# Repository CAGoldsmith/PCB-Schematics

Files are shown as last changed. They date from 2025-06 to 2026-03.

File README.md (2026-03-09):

# Drosophibot II PCBs
Power and signal PCBs for the biomimetic fruit fly robot Drosophibot II. More information about Drosophibot II can be found in [Goldsmith et al. 2024](https://iopscience.iop.org/article/10.1088/1748-3190/ad80ec) and [Goldsmith 2025](https://researchrepository.wvu.edu/etd/12842/). CAD files for the robot can be found in the [`Drosophibot-II-CAD`](https://github.com/CAGoldsmith/Drosophibot-II-CAD) repository.

This repository contains:
- ZIP files of the Gerber and drill files necessary to manufacture each board
- PDFs with renders and schematics of the boards
- A `.f3z` file of each board containing the design files from Fusion

## Board functions
### 18 Position OpenCM MUX
An 18 position demultiplexer (routing 18 signals into 6 analog ports) for the Robotis OpenCM9.04 microcontroller. Designed to sit on top of the microcontroller as a shield.

### 36 Position OpenCM MUX
A 36 position demultiplexer (routing 36 signals into 6 analog ports, one for each robot leg) for the Robotis OpenCM9.04 microcontroller. Designed to sit on top of the microcontroller as a shield. Additionally includes multiplexing of the board's I2C ports to route the signal to each leg.

### Six Strain Amplifier
Board intended to amplify and route six analog strain signals, as well as digitally calibrate the rest level of each signal. It contains a Wheatstone bridge circuit for each signal with a digital-potentiometer (digipot) included for bridge balancing via I2C connection from the robot's microcontroller. Each strain signal is then routed into an instrumentation amplifier for amplification before being output. Analog switches are used to multiplex the I2C signal to one half of the board at a time (necessitated by the limited possible unique digipot IDs).  

### Drosophibot Power Board
Board to supply power from the offboard power supply and route the Serial control signal from the robot's computer to all of the robot's actuators. Includes power indicator LEDs as well as removable shunts to easily add/remove power to each leg.

## Editing in Autodesk Fusion 360
Download the relevant board's `.f3z` file and open it in Fusion to import the design files. 

## Manufacturing
Download the "<board name>_CamFiles" zip file for the desired board in the board's "CAMOutputs" folder. For example, for the 36 Position OpenCM MUX, the required file would be "36PosMUX_CamFiles.zip." All boards were designed with professional PCB manufacturing in mind, so the Design Rules may need to be changed in Autodesk for places with less capability (e.g., campus makerspaces).

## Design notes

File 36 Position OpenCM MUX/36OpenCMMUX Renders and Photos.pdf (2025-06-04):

B)

A)

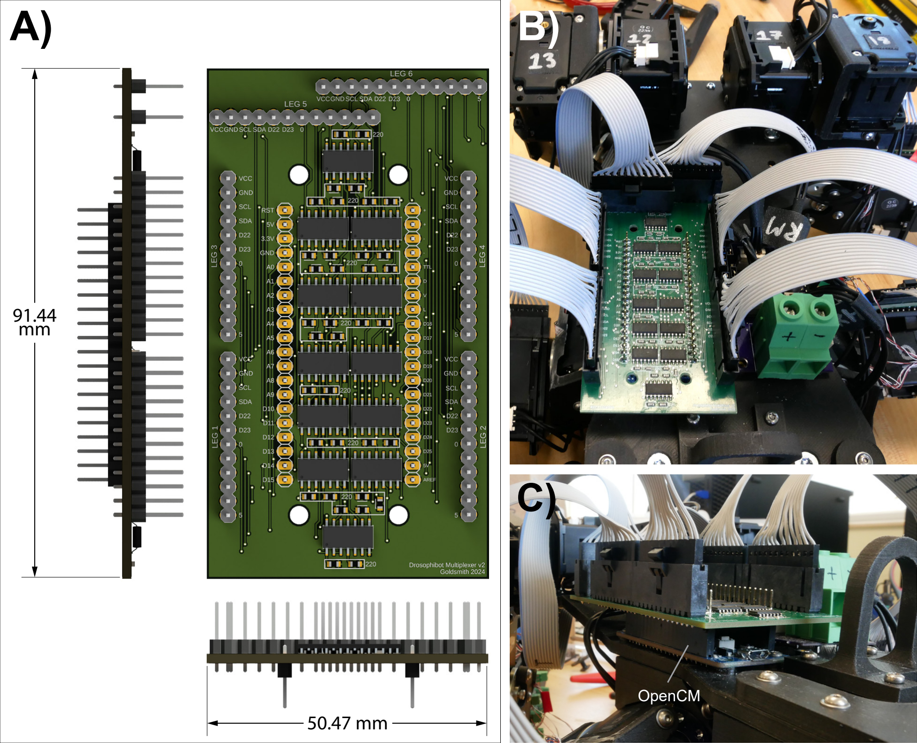
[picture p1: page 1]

Image of how deMUX slots onto OpenCM

50.47 mm

91.44
mm

C)

OpenCM

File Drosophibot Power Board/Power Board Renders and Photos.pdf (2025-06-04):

B)

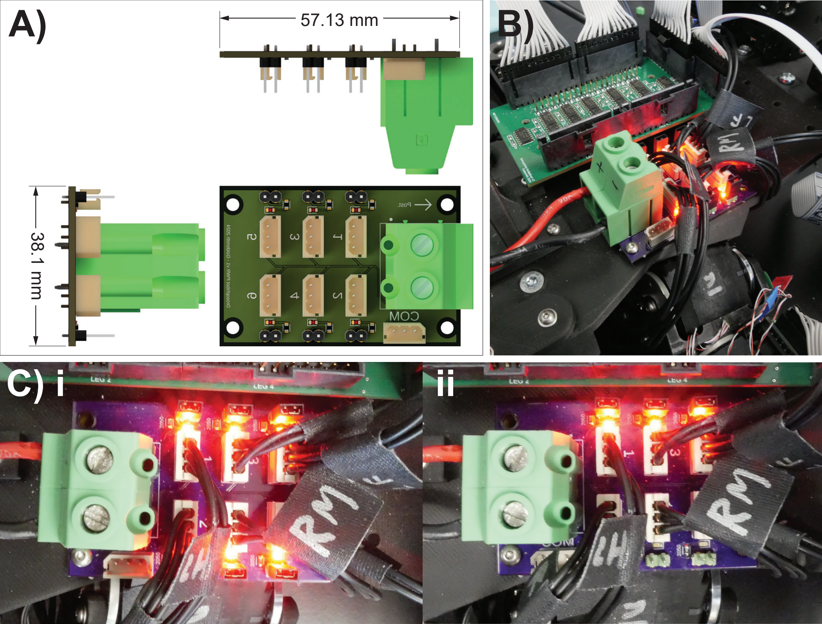
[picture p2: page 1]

38.1 mm

A) 57.13 mm
C) i | ii

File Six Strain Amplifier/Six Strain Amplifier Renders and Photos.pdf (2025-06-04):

A) B)

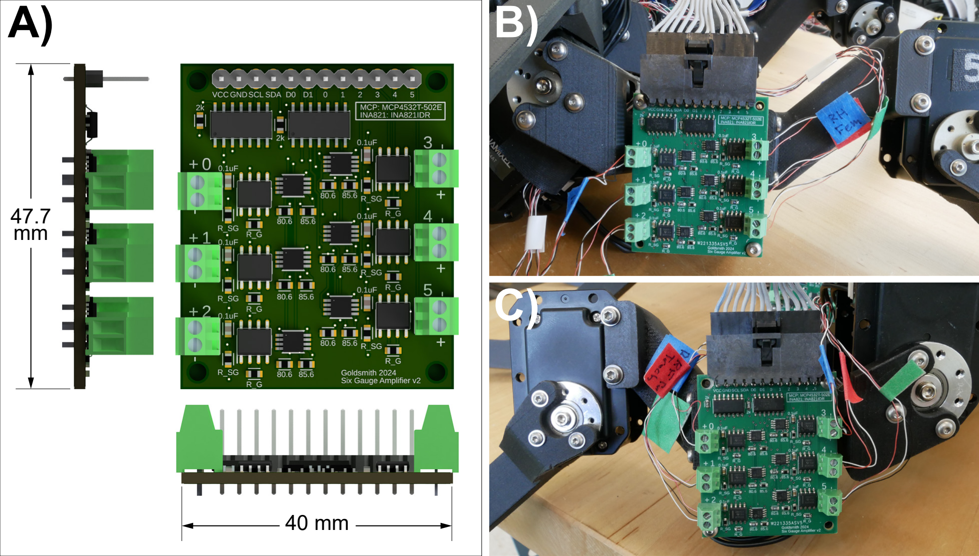
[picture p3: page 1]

47.7
mm

40 mm

C)

Image of circuit board on
multiple legs

C)

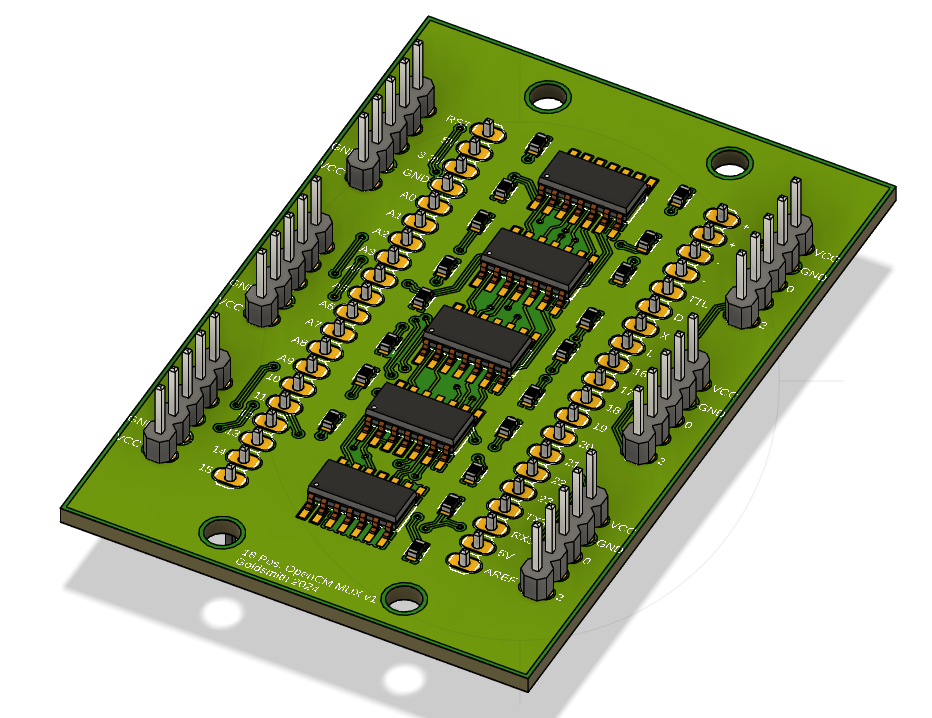
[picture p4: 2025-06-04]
18 Position OpenCM MUX/18 Pos OpenCM MUX Top Render.png

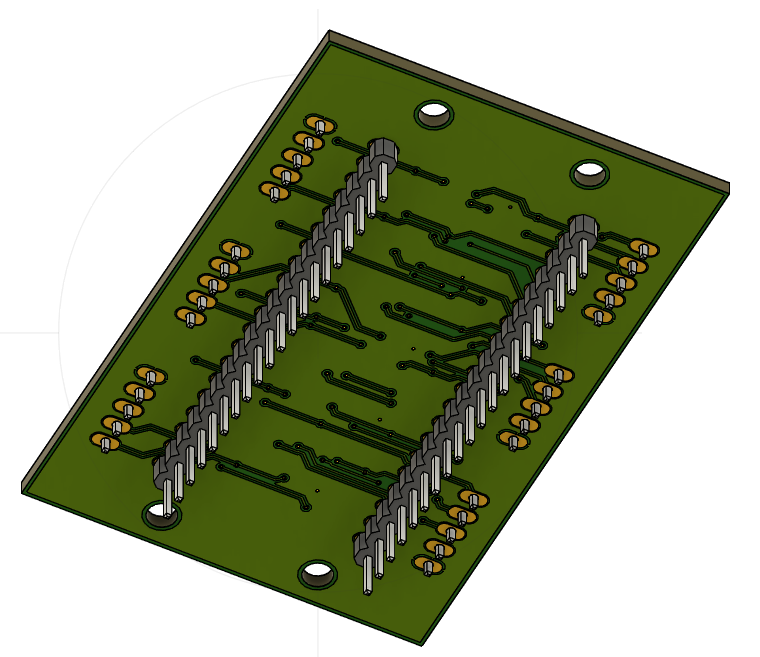
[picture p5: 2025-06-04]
18 Position OpenCM MUX/18 Pos OpenCM MUX Bottom Render.png

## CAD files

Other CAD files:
Drosophibot Power Board/Drosophibot Power Board v44.f3z

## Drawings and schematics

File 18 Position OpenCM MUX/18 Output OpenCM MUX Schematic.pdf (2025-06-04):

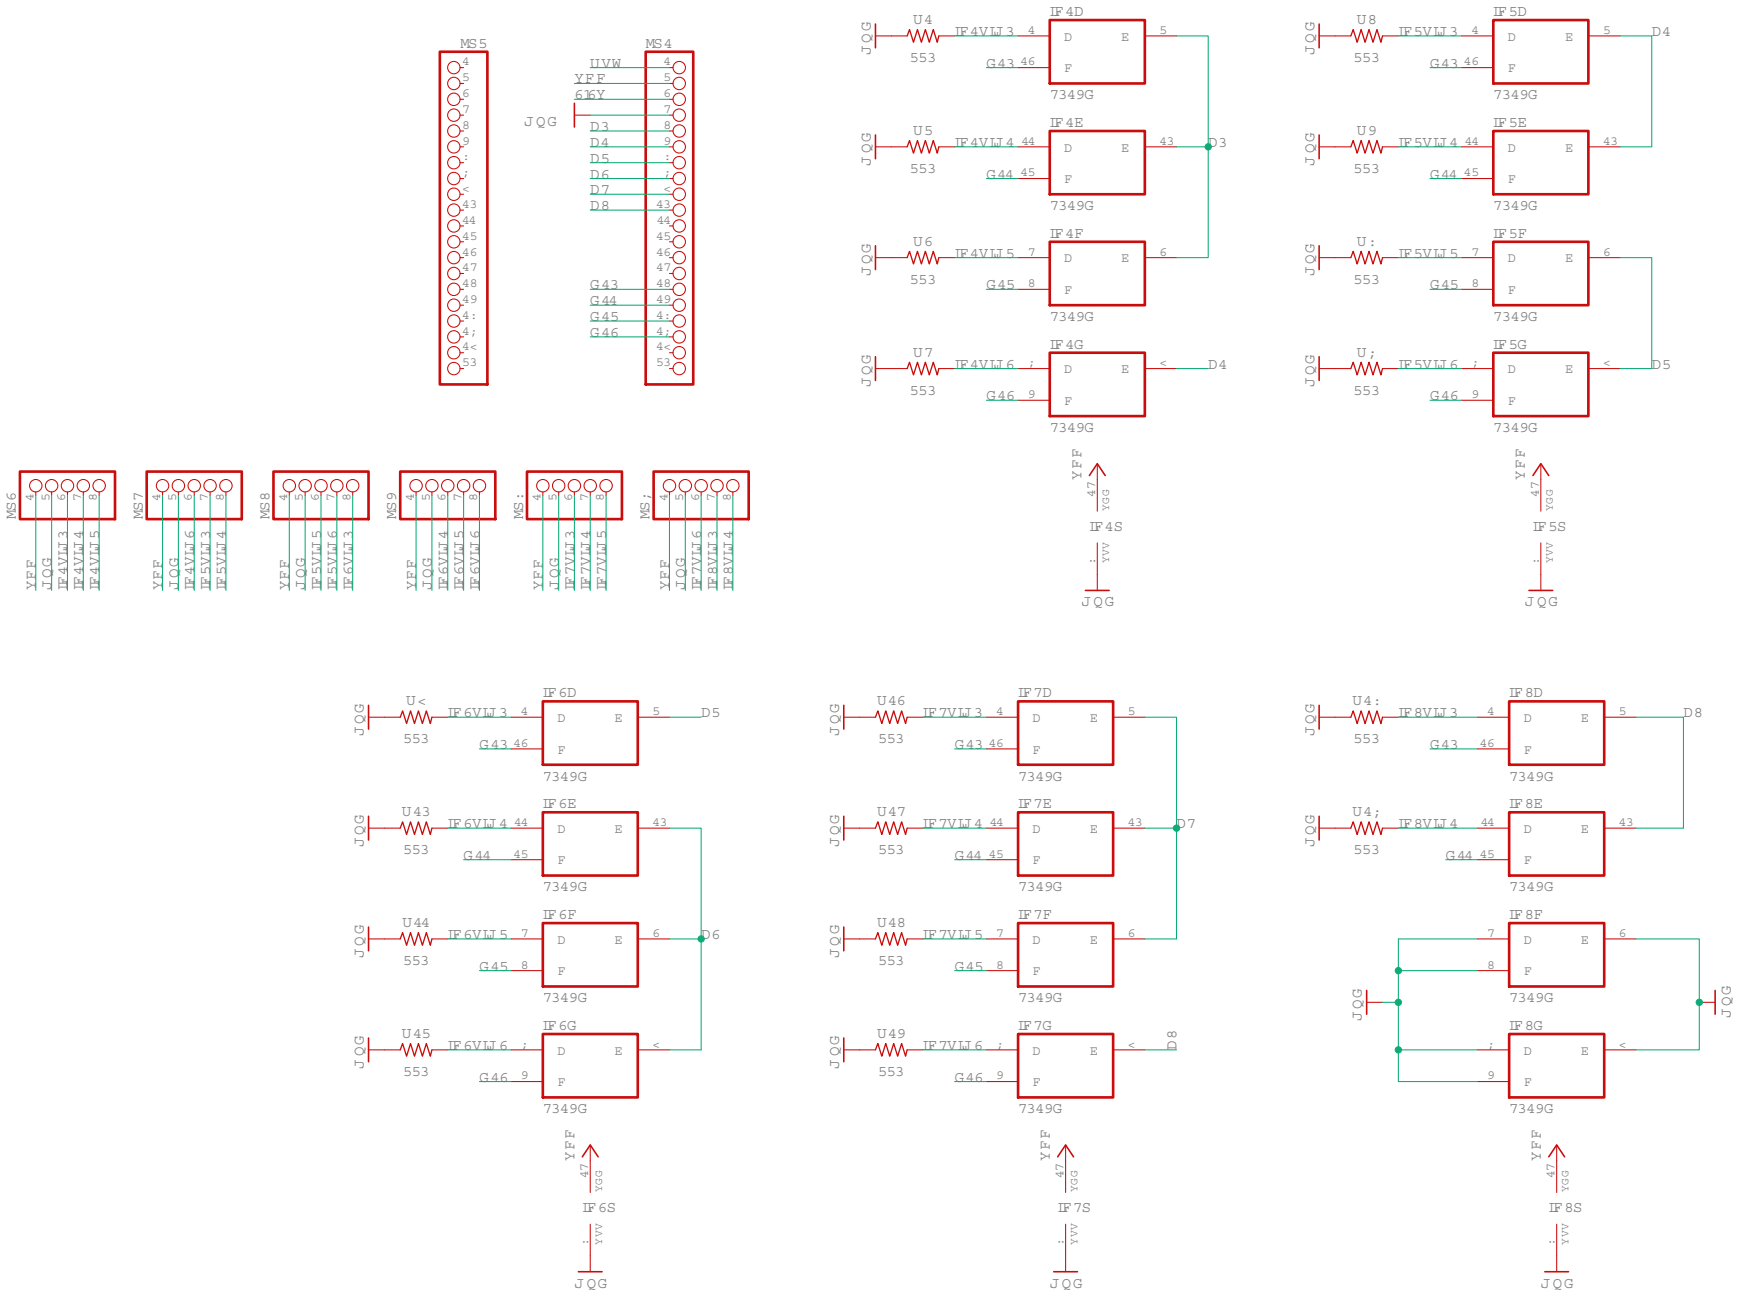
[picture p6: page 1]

GND GND

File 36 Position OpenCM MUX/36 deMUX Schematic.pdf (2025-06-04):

## 36 INPUT DEMUX CIRCUIT

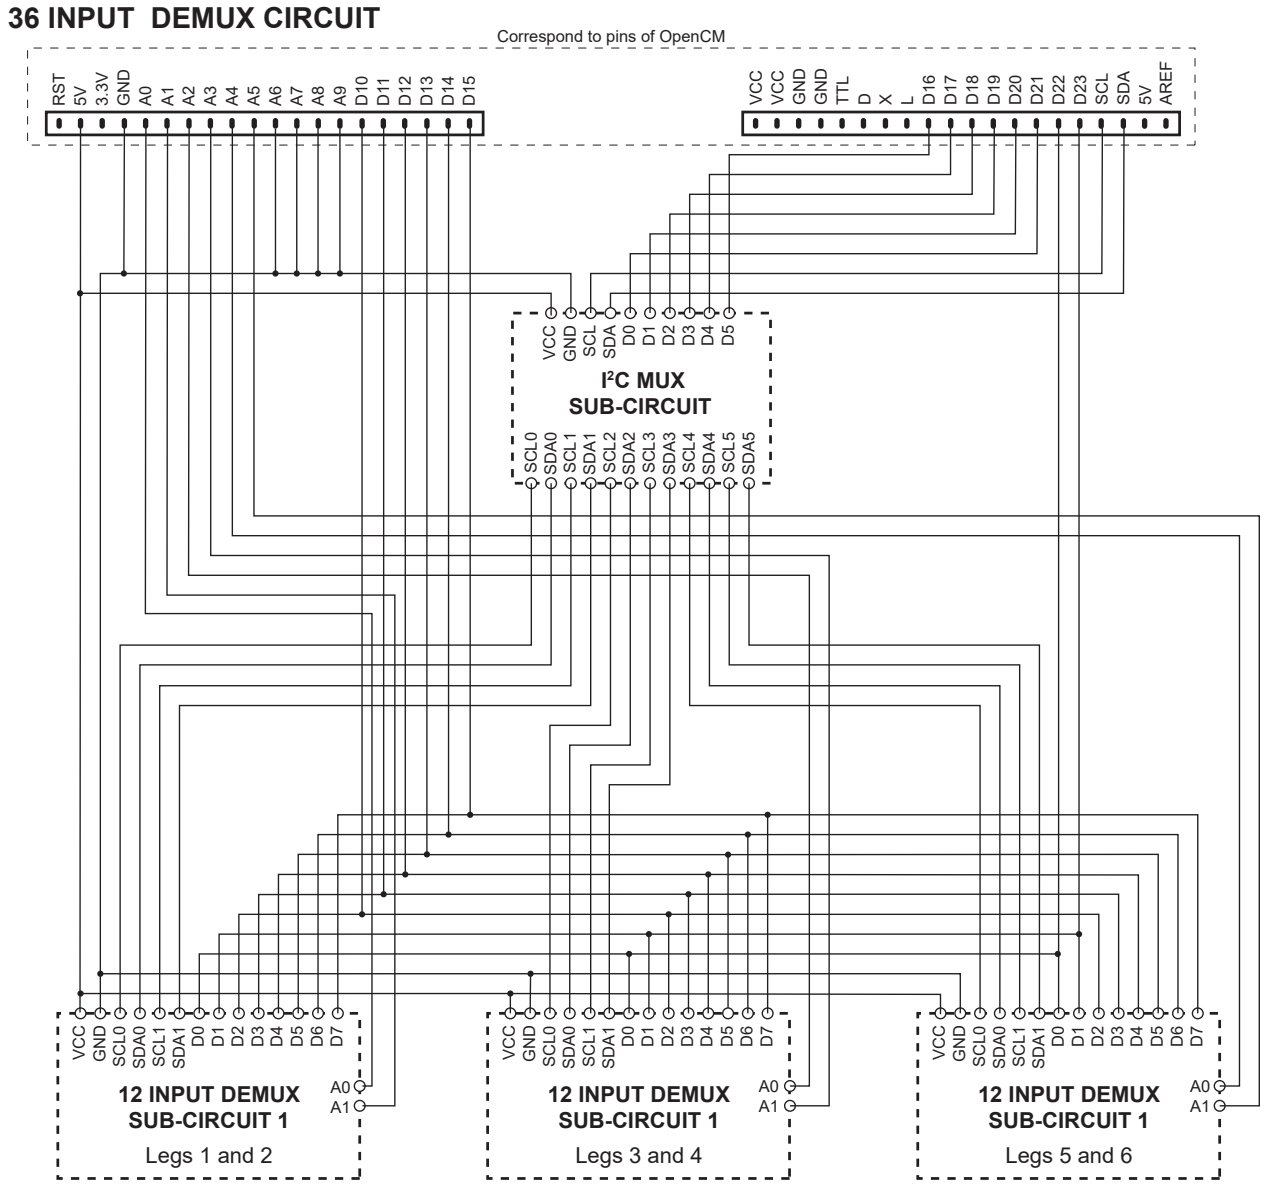
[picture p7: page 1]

Correspond to pins of OpenCM

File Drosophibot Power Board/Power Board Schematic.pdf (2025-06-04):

# DROSOPHIBOT II POWER SUPPLY BOARD

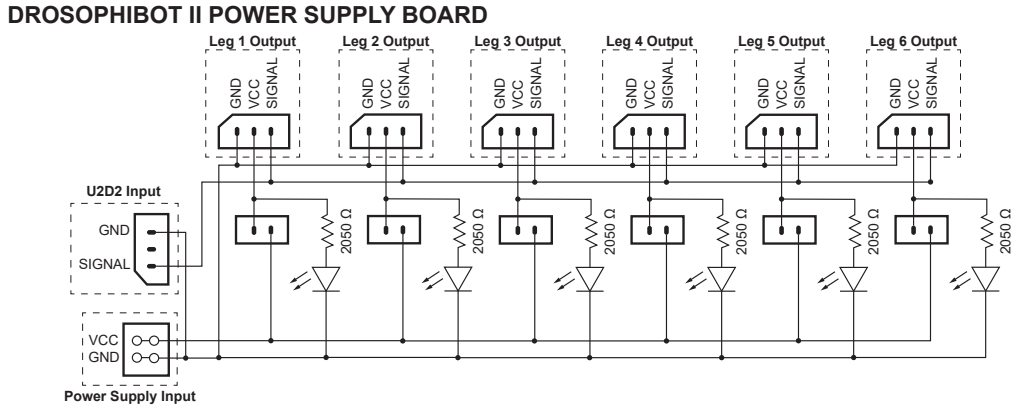
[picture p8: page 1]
GND; SIGNAL; GND VCC; VCC GND; U2D2 Input; Leg 1 Output; Leg 2 Output; Leg 3 Output; Leg 4 Output; Leg 5 Output; Leg 6 Output

Power Supply Input

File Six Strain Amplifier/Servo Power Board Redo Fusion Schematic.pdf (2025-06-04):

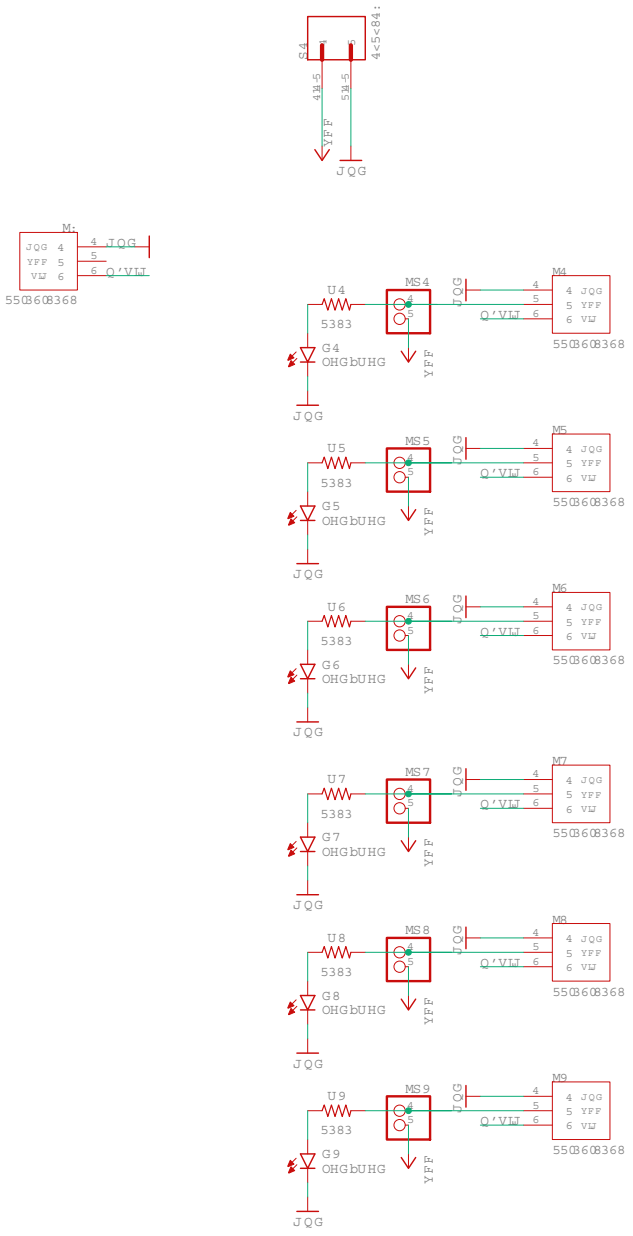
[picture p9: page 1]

GND GND GND

VCC VCC VCC

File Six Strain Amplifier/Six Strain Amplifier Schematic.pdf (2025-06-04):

### SIX STRAIN GAUGE AMPLIFIER

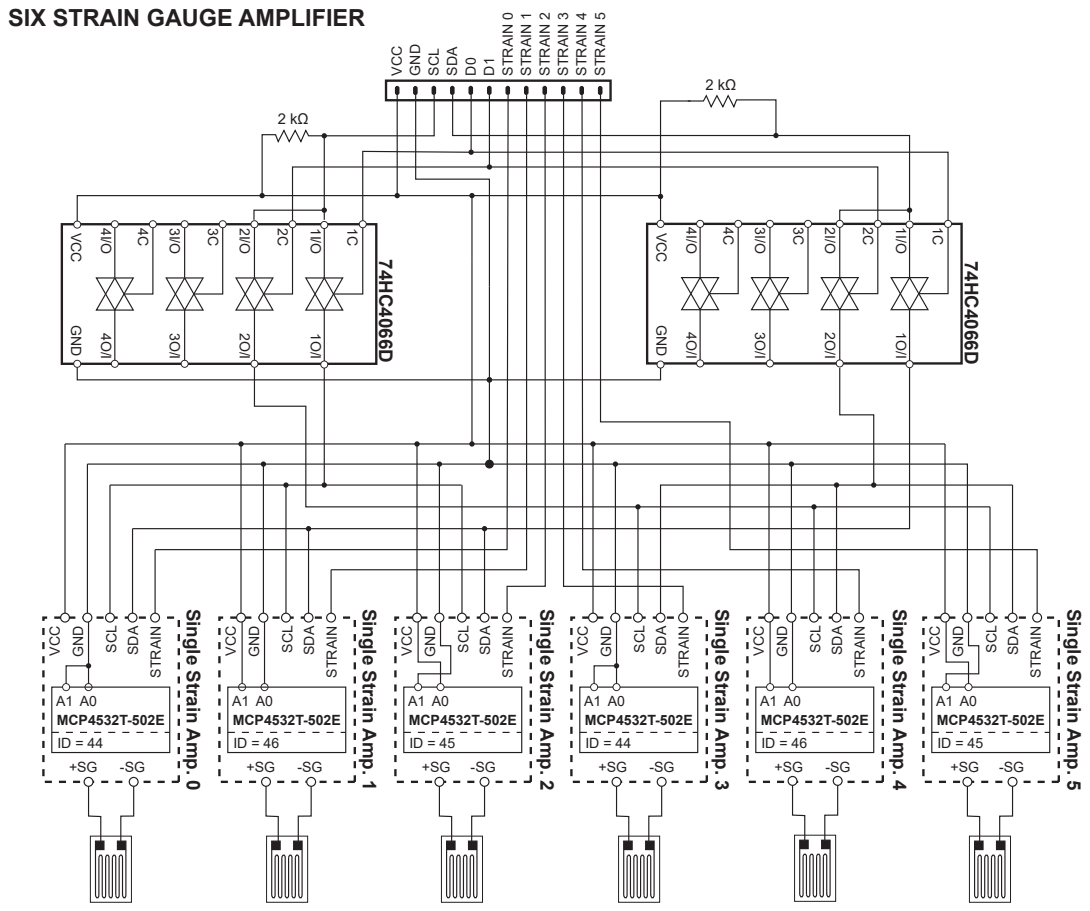
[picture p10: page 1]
VCC; GND; SCL; SDA; STRAIN; MCP4532T-502E; GND SCL; SDA D0; STRAIN 0; STRAIN 1; STRAIN 2; STRAIN 3; STRAIN 4; STRAIN 5; VCC GND

Single Strain Amp. 0

Single Strain Amp. 1

Single Strain Amp. 2

Single Strain Amp. 3

Single Strain Amp. 4

Single Strain Amp. 5

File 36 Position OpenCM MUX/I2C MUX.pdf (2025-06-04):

I
2

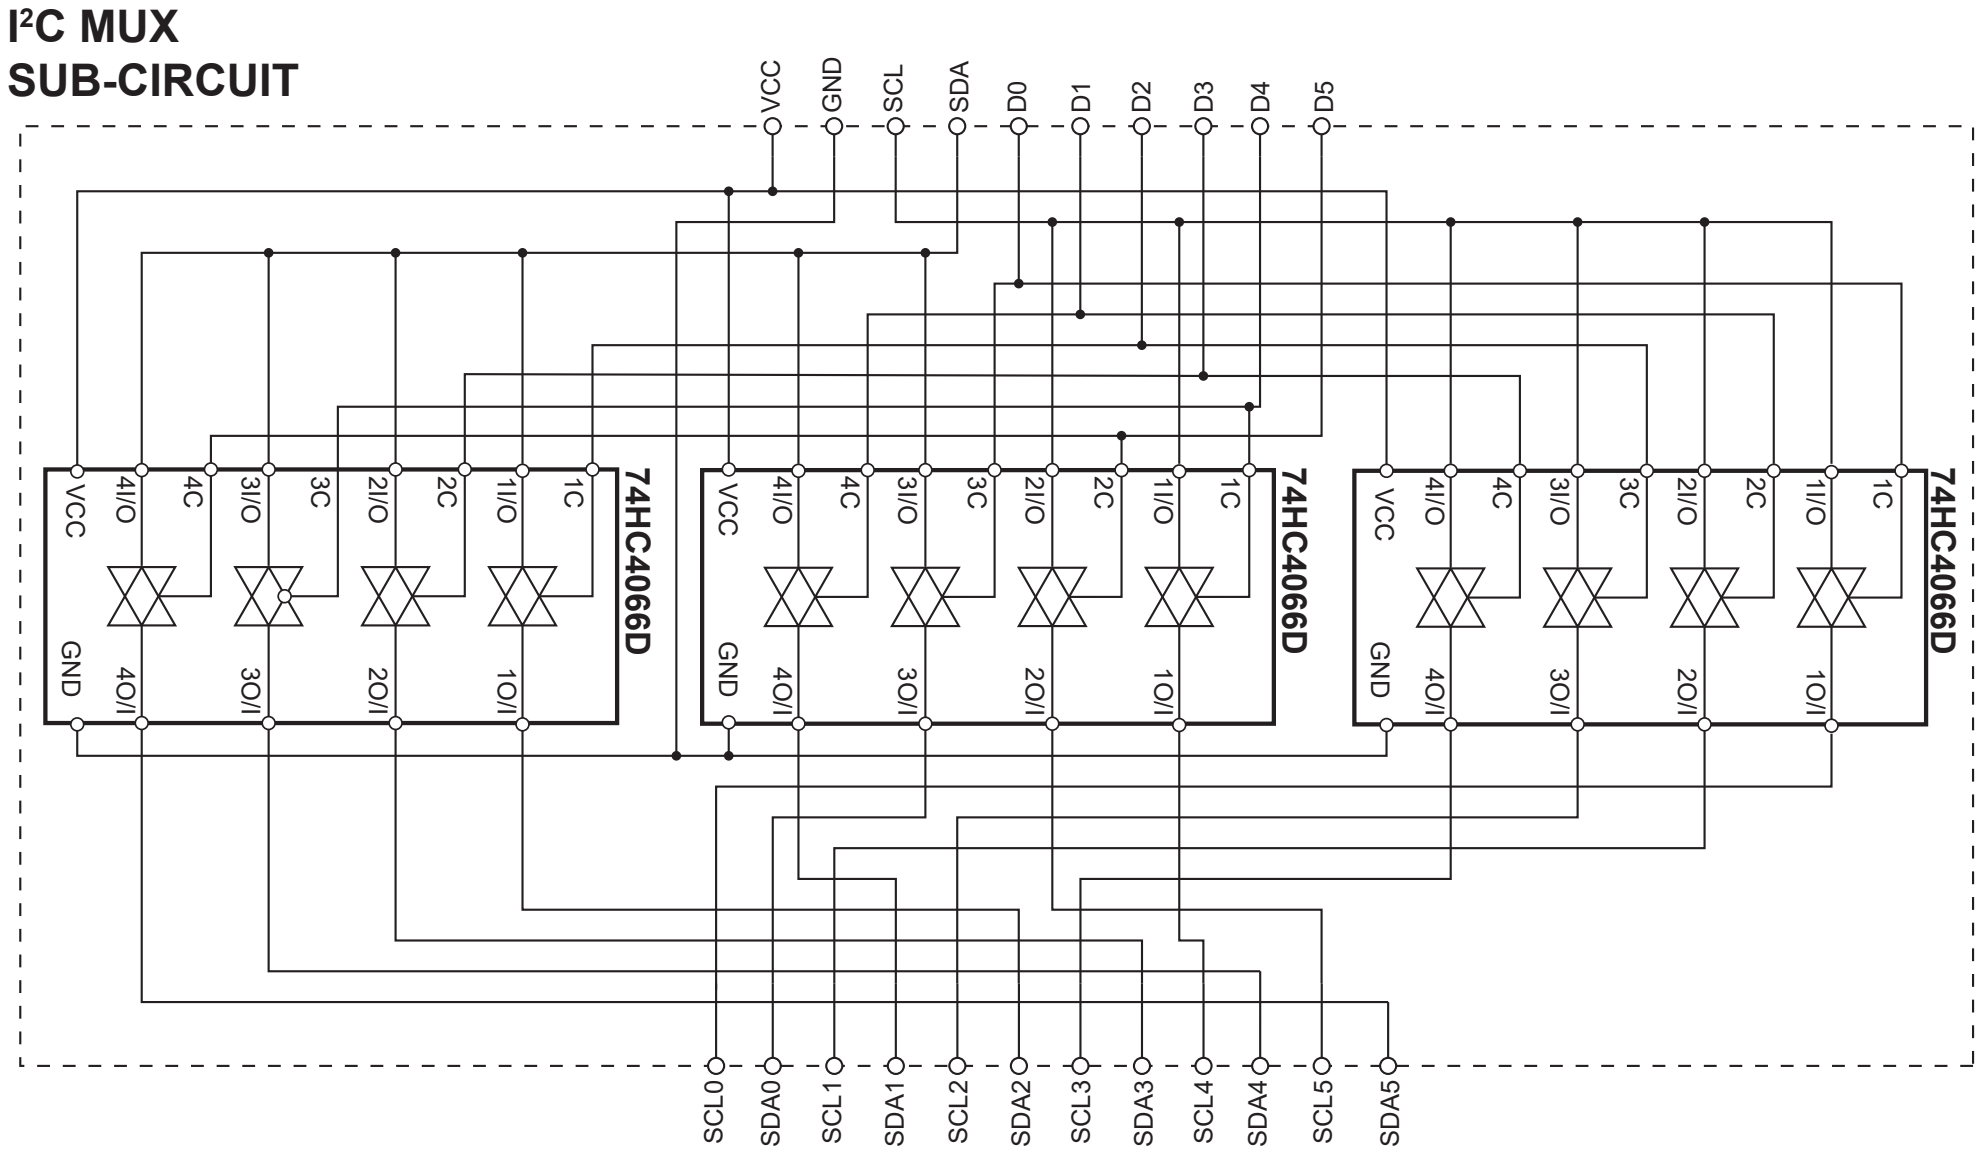
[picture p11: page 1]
C MUX SUB-CIRCUIT; VCC; GND; SCL; SDA; SCL0; SDA0; SCL1; SDA1; SCL2; SDA2; SCL3; SDA3; SCL4; SDA4; SCL5; SDA5; VCC GND

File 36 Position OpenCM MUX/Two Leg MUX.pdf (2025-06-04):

# 12 INPUT DEMUX SUB-CIRCUIT

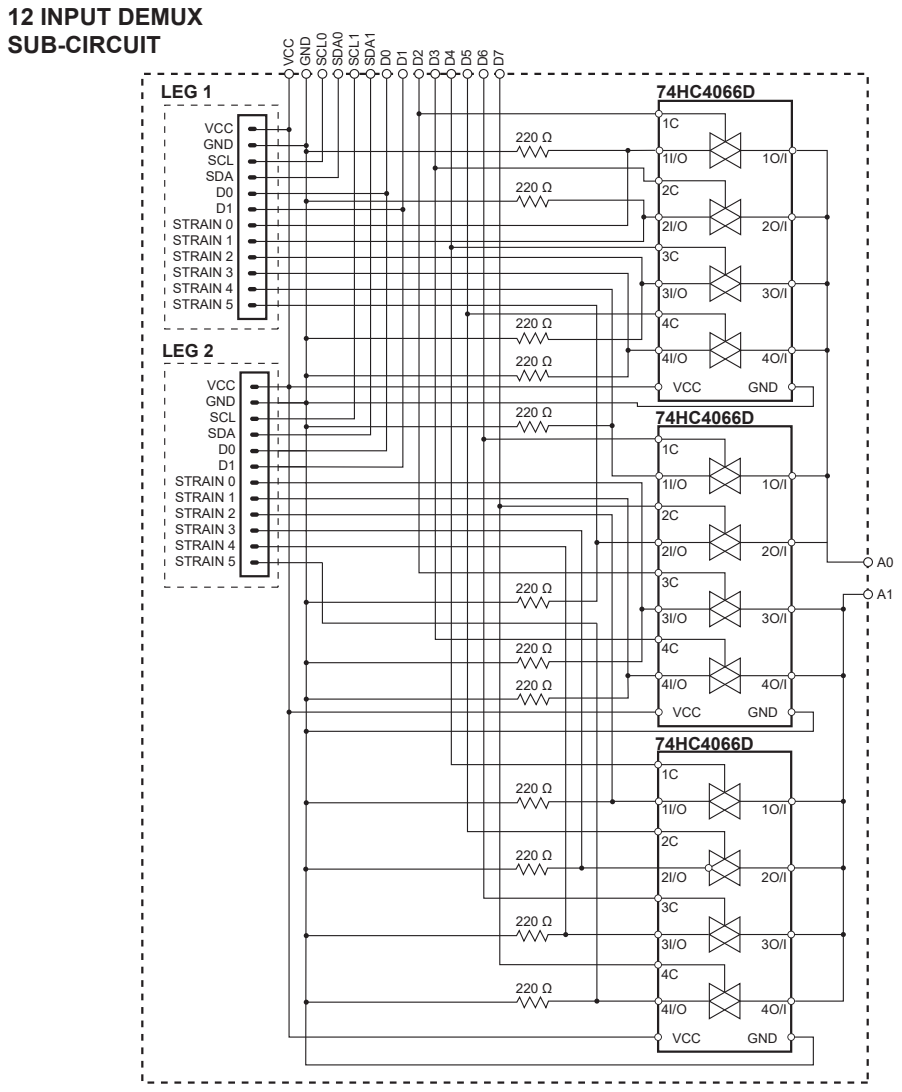
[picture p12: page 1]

LEG 1 | | 74HC4066D

1O/I 2O/I 3O/I 4O/I GND

220 Ω | 4I/O VCC

1O/I
2C

3I/O
4C

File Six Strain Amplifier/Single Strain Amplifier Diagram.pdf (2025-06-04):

# SINGLE STRAIN GAUGE AMPLIFIER SUB-CIRCUIT

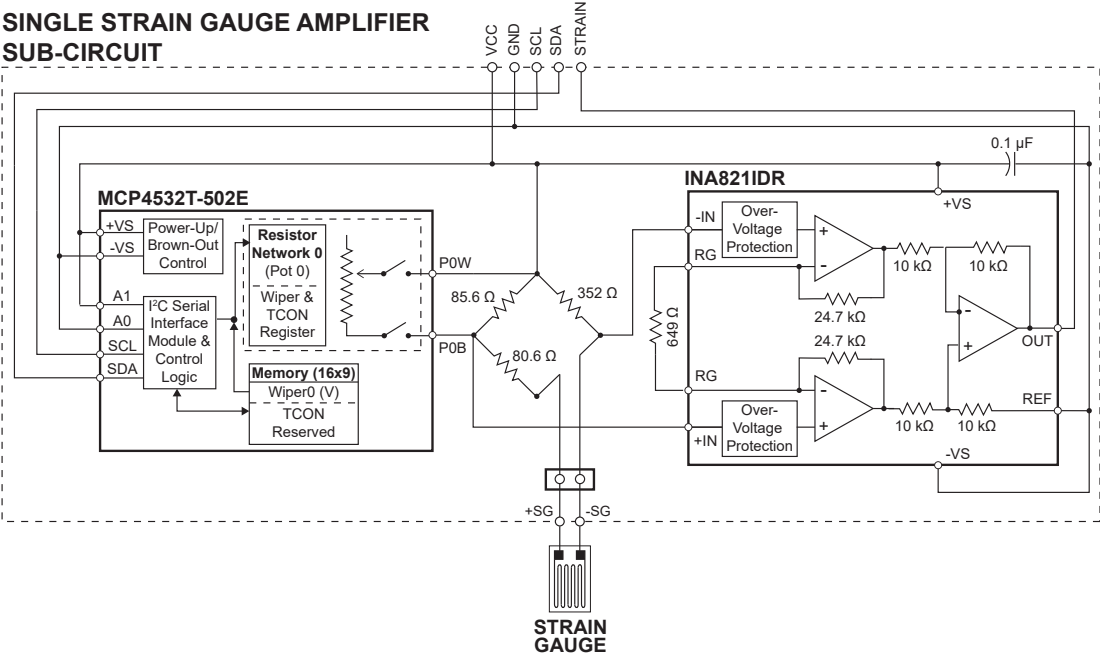
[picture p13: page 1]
Over- Voltage Protection; REF; OUT; INA821IDR; Power-Up/ Brown-Out Control; C Serial Interface Module & Control Logic; A1 A0 SCL; SDA; Memory (16x9); Resistor Network 0 (Pot 0) Wiper & TCON Register; Wiper0 (V) TCON Reserved; MCP4532T-502E; STRAIN GAUGE; VCC; GND; SCL; STRAIN

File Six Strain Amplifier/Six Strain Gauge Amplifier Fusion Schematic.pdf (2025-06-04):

## INA821IDD0008A_L

## M CP4532T-502E/M SM SO P8_M C_M CH-L

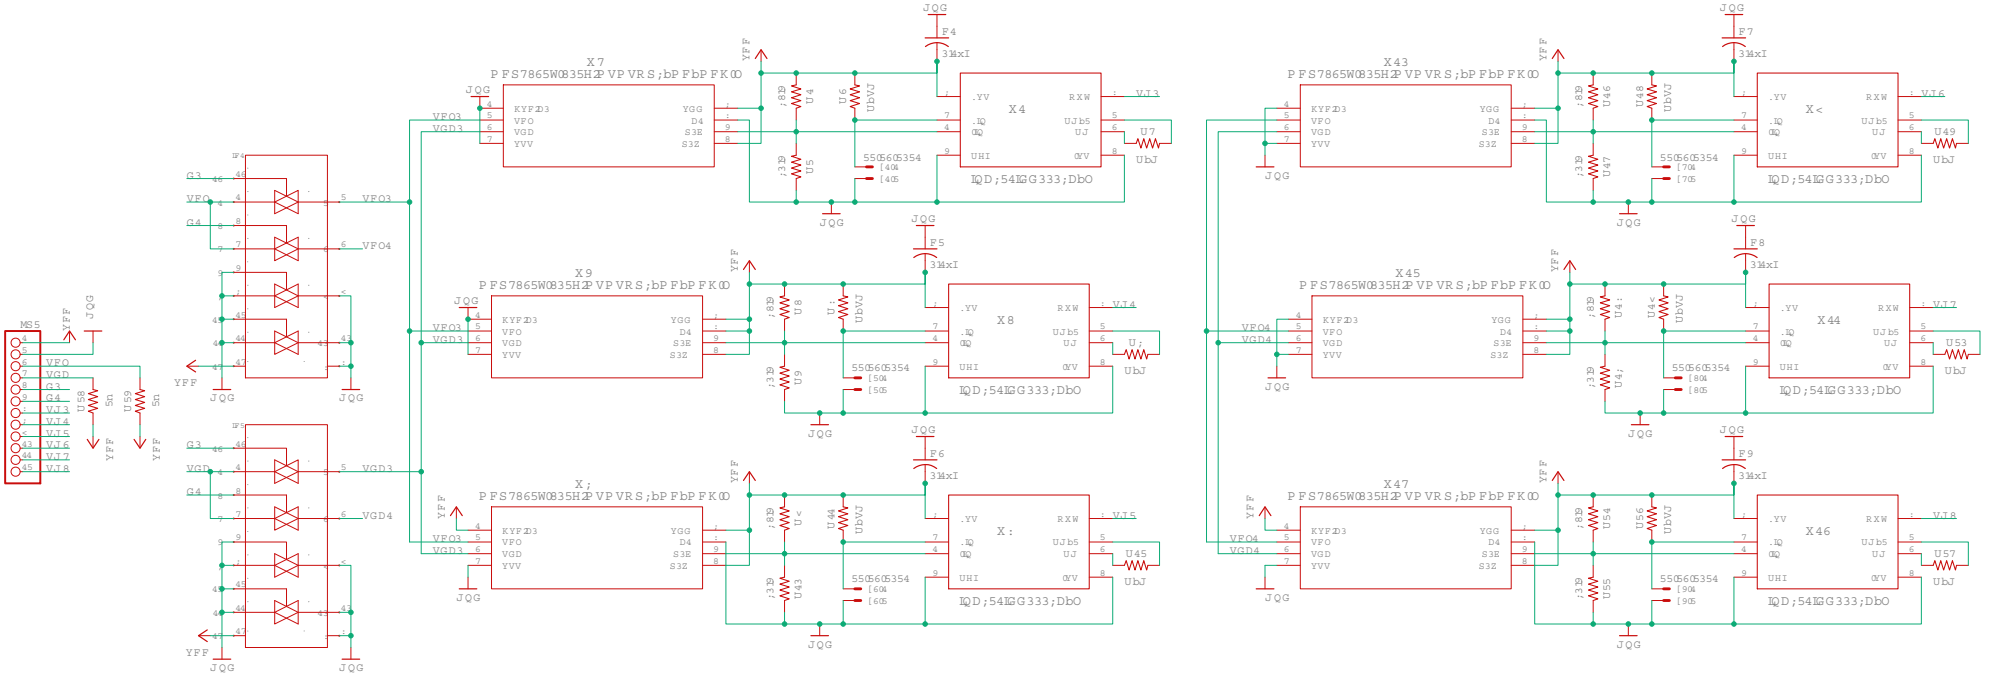
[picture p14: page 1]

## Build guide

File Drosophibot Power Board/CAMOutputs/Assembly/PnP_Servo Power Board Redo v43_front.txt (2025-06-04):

D1	28.58	1.91	180.00	LED_RED	LEDC1608X35N_FLAT-R
D2	42.55	1.91	180.00	LED_RED	LEDC1608X35N_FLAT-R
D3	56.52	1.91	180.00	LED_RED	LEDC1608X35N_FLAT-R
D4	28.58	36.20	180.00	LED_RED	LEDC1608X35N_FLAT-R
D5	42.55	36.20	180.00	LED_RED	LEDC1608X35N_FLAT-R
D6	56.52	36.20	180.00	LED_RED	LEDC1608X35N_FLAT-R
R1	25.40	1.91	180.00	2050	RESC1608X60
R2	39.37	1.91	180.00	2050	RESC1608X60
R3	53.34	1.91	180.00	2050	RESC1608X60
R4	25.40	36.20	180.00	2050	RESC1608X60
R5	39.37	36.20	180.00	2050	RESC1608X60
R6	53.34	36.20	180.00	2050	RESC1608X60

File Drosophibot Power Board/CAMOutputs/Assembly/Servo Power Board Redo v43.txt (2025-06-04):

Partlist exported from Fusion Hub: WVU NeuroMINT   Project: Drosophibot II  Board: Servo Power Board Redo v43 at 6/4/2025 1:52 PM

Qty Value      Device                      Package             Parts                        Description                                                                               CATEGORY COLOR DESCRIPTION   MANUFACTURER    MAXIMUM_PACKAGE_HEIGHT MPN OPERATING_TEMP PARTREV PART_STATUS POPULARITY RATING ROHS_COMPLIANT SERIES STANDARD                     SUB-CATEGORY THERMALLOSS TOLERANCE TYPE     VALUE  
6              PINHD-1X2                   1X02                JP1, JP2, JP3, JP4, JP5, JP6 PIN HEADER                                                                                                                                                                                           98                                                                                                                      
1   1929517    1929517                     PHOENIX_1929517     P1                           Conn Terminal Block 2 POS 10.16mm Solder ST Thru-Hole 57A                                                              Phoenix Contact                                                                                                                                                                                       
6   2050       R-US_CHIP-0603(1608-METRIC) RESC1608X60         R1, R2, R3, R4, R5, R6       Resistor Fixed - ANSI                                                                     Resistor                                                                                                                                                                        Fixed                                              
7   22-03-5035 22-03-5035                  MOLEX_22-03-5035    J1, J2, J3, J4, J5, J6, J7   2.50mm Pitch SPOX™ Wire-to-Board Header, Vertical, Shrouded, 3 Circuits, Tin (Sn) Plating                              Molex           5.9mm                                     B                                                           Manufacturer recommendations                                                    
6   LED_RED    CHIP-FLAT-R_0603-0.35MM     LEDC1608X35N_FLAT-R D1, D2, D3, D4, D5, D6                                                                                                 LED      RED   CHIP LED FLAT                                                                                                                                                    CHIP                               FLAT_TOP LED_RED

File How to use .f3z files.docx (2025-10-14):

https://fileinfo.com/extension/f3z

These individual files need to be imported into Fusion 360, which will then give you access to all of the design files.

To do so:

- Open Fusion 360
- Go to File > Upload…
- Select the .f3z file, choose your desired location, then Upload.

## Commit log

2025-06-11 added .f3z files
    [Drosophibot Power Board v44.f3z]
2025-10-20 fixed display of R35-6 values
    [copper_bottom.gbr, copper_top.gbr, drill_1_16.xln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]
